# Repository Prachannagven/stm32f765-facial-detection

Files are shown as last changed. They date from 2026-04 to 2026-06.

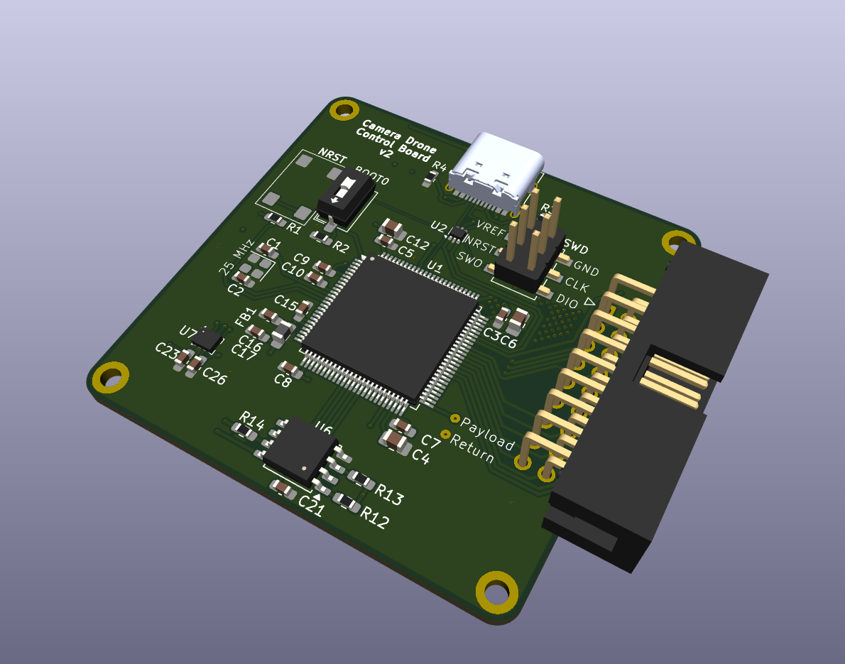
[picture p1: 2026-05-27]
pcb/kamikaze-drone/images/v2/3D_Angled.png

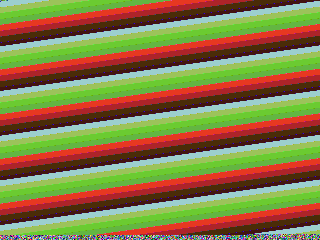
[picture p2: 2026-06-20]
firmware/ov7670_camera/Python/captures/20260612_212751.png

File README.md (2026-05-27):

# Introduction
The goal of this project is to build a 50x50mm drone, capable of autonomous flight, and recognizing humans. The final product should be able to fly towards the target.

For current protyping, I'm looking at using an OV7670 camera, which supplies up to a 320x260 frame, based on the qvga output. However, I can go as low as the qcif resolution (176x144), although I'm not sure recognition will work well on that.

# Links to Look at
[OV7670 Interfacing][https://www.youtube.com/watch?v=aanNau1RDTA]

# Hardware Design
I use an STM32F765VIT6 due to its on board DCMI block, as well as its ART accelerator to speed up computations. It pairs with a TOF sensor, a BMP280 barometer, IMU and magnetic field sensor for full attitude determination.

Four brushed DC motors are used for this system, allowing for lightweight control. The only limitation here is how heavy the entire system is going to be. It can carry approximately 100-200 grams, which is well within our weight budget.

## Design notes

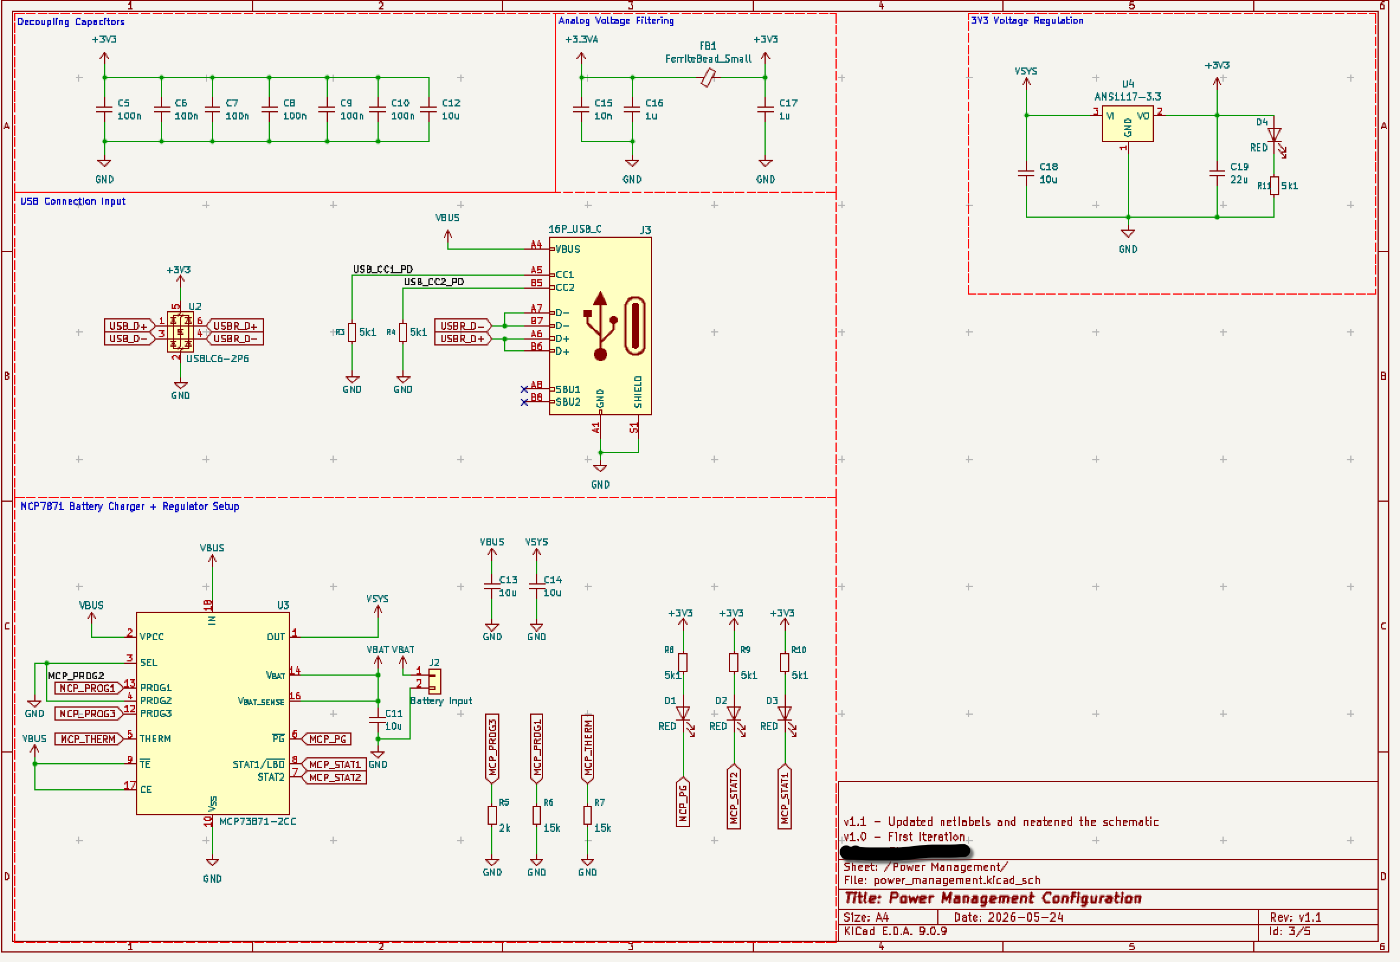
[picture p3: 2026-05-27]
pcb/kamikaze-drone/images/v2/Sch_PowerManagement.png

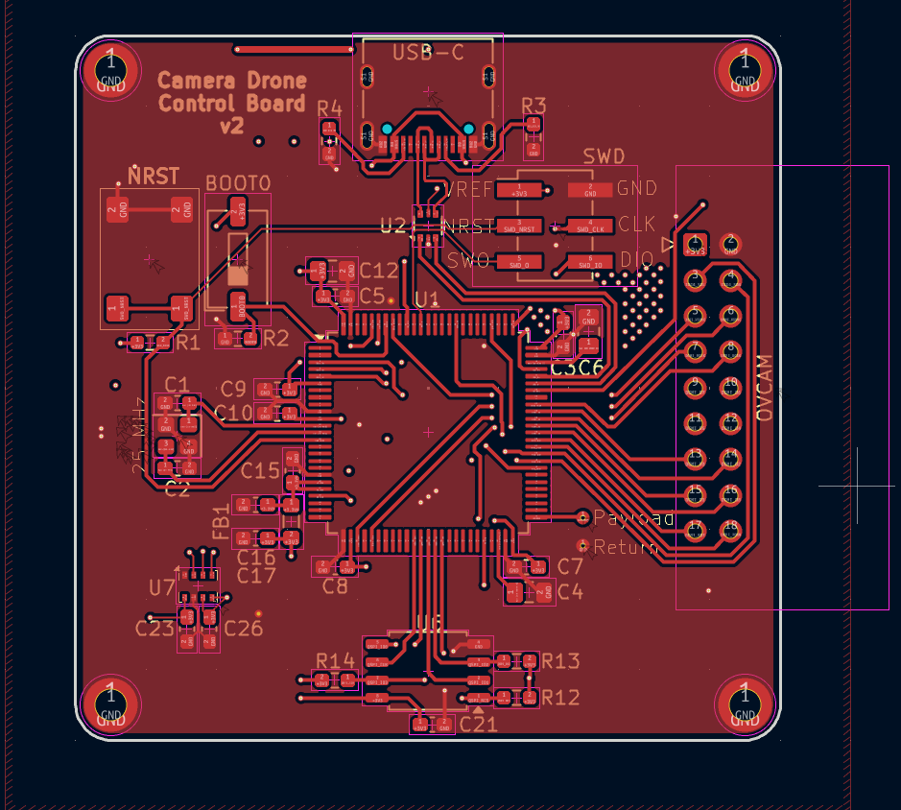
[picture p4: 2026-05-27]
pcb/kamikaze-drone/images/v2/PCB_FrontStandard.png

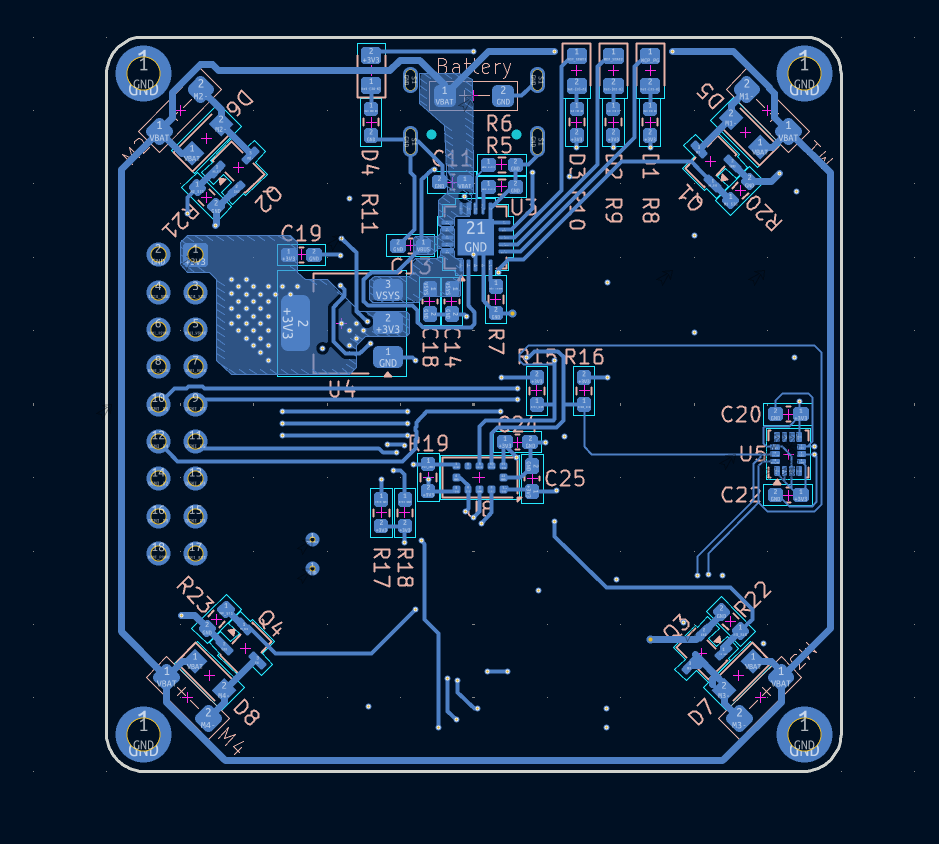
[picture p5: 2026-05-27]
pcb/kamikaze-drone/images/v2/PCB_BackStandard.png

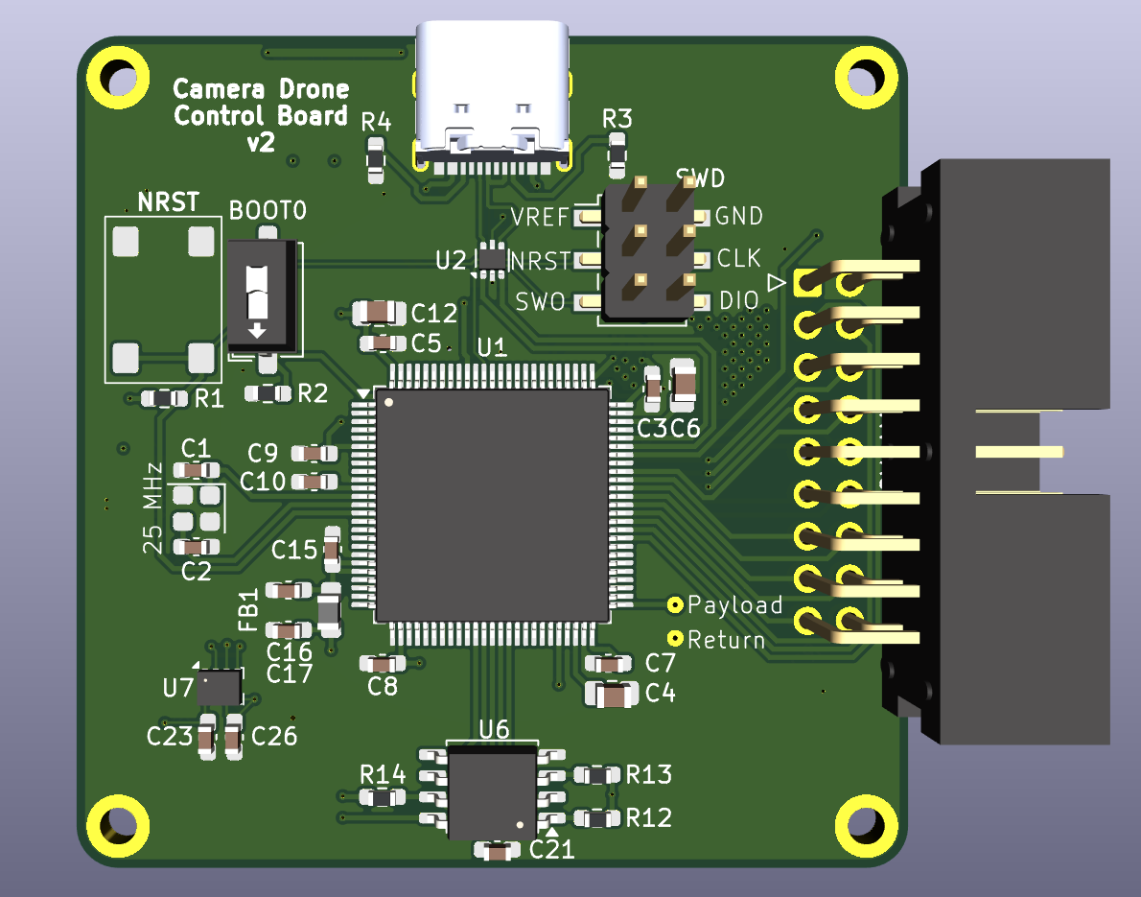
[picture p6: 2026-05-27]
pcb/kamikaze-drone/images/v2/3D_Front.png

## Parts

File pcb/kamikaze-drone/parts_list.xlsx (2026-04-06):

S. No. | Item | Spec | Cost | Communication Protocol | Link 1 | Vendor | Selected Comms
1 | Main MCU | STM32F765VIT6 | 794 | N/A | https://robu.in/product/stm32f765vit6-stmicroelectronics-arm-mcu-arm-cortex-m7-microcontrollers-arm-cortex-m7-32-bit-216-mhz-2-mb-100-pins/ | Robu | N/A
2 | IMU | LSM6DSLTR | 178 | SPI or I2C | https://robu.in/product/lsm6dsltr-stmicroelectronics-mems-module-inemo-lsm6d-series-imu-1-71-v-to-3-6-v-%c2%b1-16g-lga-14/ | Robu | I2C
3 | Barometer | BMP280 | 33 | I2C | https://robu.in/product/bmp280-barometric-pressure-and-altitude-sensor-i2c-spi-module/ | Robu | I2C
4 | EEPROM | M95512 | 62 | SPI | https://robu.in/product/m95512-rmn6p-eeprom-512-kbit-64k-x-8bit-serial-spi-16-mhz-soic-8-pins/ | Robu | SPI
5 | Magnetometer | QMC5883L | 317 | I2C | https://www.flyrobo.in/qmc5883l-qfn-16-three-axis-magnetic-sensor-chip?search=qmc5883l&description=true | FlyRobo | I2C
6 | GPS | Neo-6M | 272 | UART | https://robu.in/product/ublox-neo-6m-gps-module/ | Robu | UART
 | 16 Mhz Crystal | YSX321SL | 20 | N/A | https://robu.in/product/ysx321sl-16mhz-18pf-10ppm-4pins-smd-smt-metal-surface-quartz-crystal-pack-of-2/ | Robu | N/A
 | LDO | AMS1117-ADJ | 9 | N/A | https://robu.in/product/ams1117-adj-1a-sot-223-voltage-regulator-ic-pack-of-5-ics/
 |  |  | 1656

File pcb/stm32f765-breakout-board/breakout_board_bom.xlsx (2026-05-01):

Robu SKU | Reference | Qty | Value | Bought | Cost | Total
595331 | C1,C2 | 2 | 10p | 10 | 1.8 | 18 | 18
595344 | C3,C4,C5,C6,C7,C8,C13 | 9 | 100n | 50 | 0.7 | 35 | 53
1544904 | C9, C14, C15 | 1 | 10u | 10 | 13 | 130 | 183
595338 | C10 | 1 | 10n | 10 | 5 | 50 | 233
R139421 | C11,C12 | 2 | 1u | 20 | 1.34 | 26.8 | 259.8
R136885 | C16,C17 | 2 | 2.2u | 20 | 1.86 | 37.2 | 297
827887 | D1 | 1 | LED | 20 | 0.79 | 15.8 | 312.8
R112445 | FB1 | 1 | FerriteBead | 10 | 3 | 30 | 342.8
R243053 | J1 | 1 | 16P_USB_C | 10 | 29 | 290 | 632.8
1114172 | J3 | 1 | SWD | 5 | 5 | 25 | 657.8
1114172 | J4 | 1 | Conn_01x05 | 0 | 5 | 0 | 657.8
1114172 | J5 | 1 | Conn_01x04 | 0 | 5 | 0 | 657.8
1114172 | J6,J7 | 2 | Conn_01x12 | 0 | 5 | 0 | 657.8
1114172 | J8 | 1 | Conn_01x03 | 0 | 5 | 0 | 657.8
1114172 | J9 | 1 | Conn_I2C2 | 0 | 5 | 0 | 657.8
R242850 | R2 | 1 | 10k | 100 | 0.16 | 16 | 673.8
R143534 | R3,R6,R7 | 3 | 1k5 | 100 | 0.28 | 28 | 701.8
R218648 | R4,R5 | 2 | 5k1 | 50 | 0.68 | 34 | 735.8
1883759 | SW2 | 1 | SW_BOOT0 | 10 | 1.55 | 15.5 | 751.3
R151772 | U1 | 1 | STM32F765VIT6 | 2 | 794 | 1588 | 2339.3
R194437 | U2 | 1 | AMS1117-3.3 | 10 | 7 | 70 | 2409.3
R243041 | U3 | 1 | USBLC6-2SC6 | 10 | 6 | 60 | 2469.3
R233512 | Y1 | 1 | 16MHz | 10 | 10 | 100 | 2569.3
 |  |  |  |  | Parts Total | 2569.3
 |  |  |  |  | PCB Total | 981
 |  |  |  |  | Project Total | 3550.3

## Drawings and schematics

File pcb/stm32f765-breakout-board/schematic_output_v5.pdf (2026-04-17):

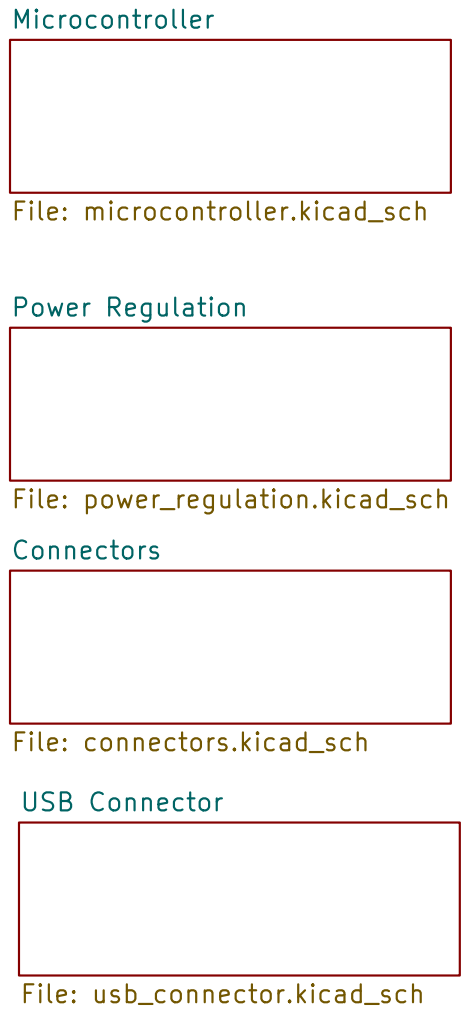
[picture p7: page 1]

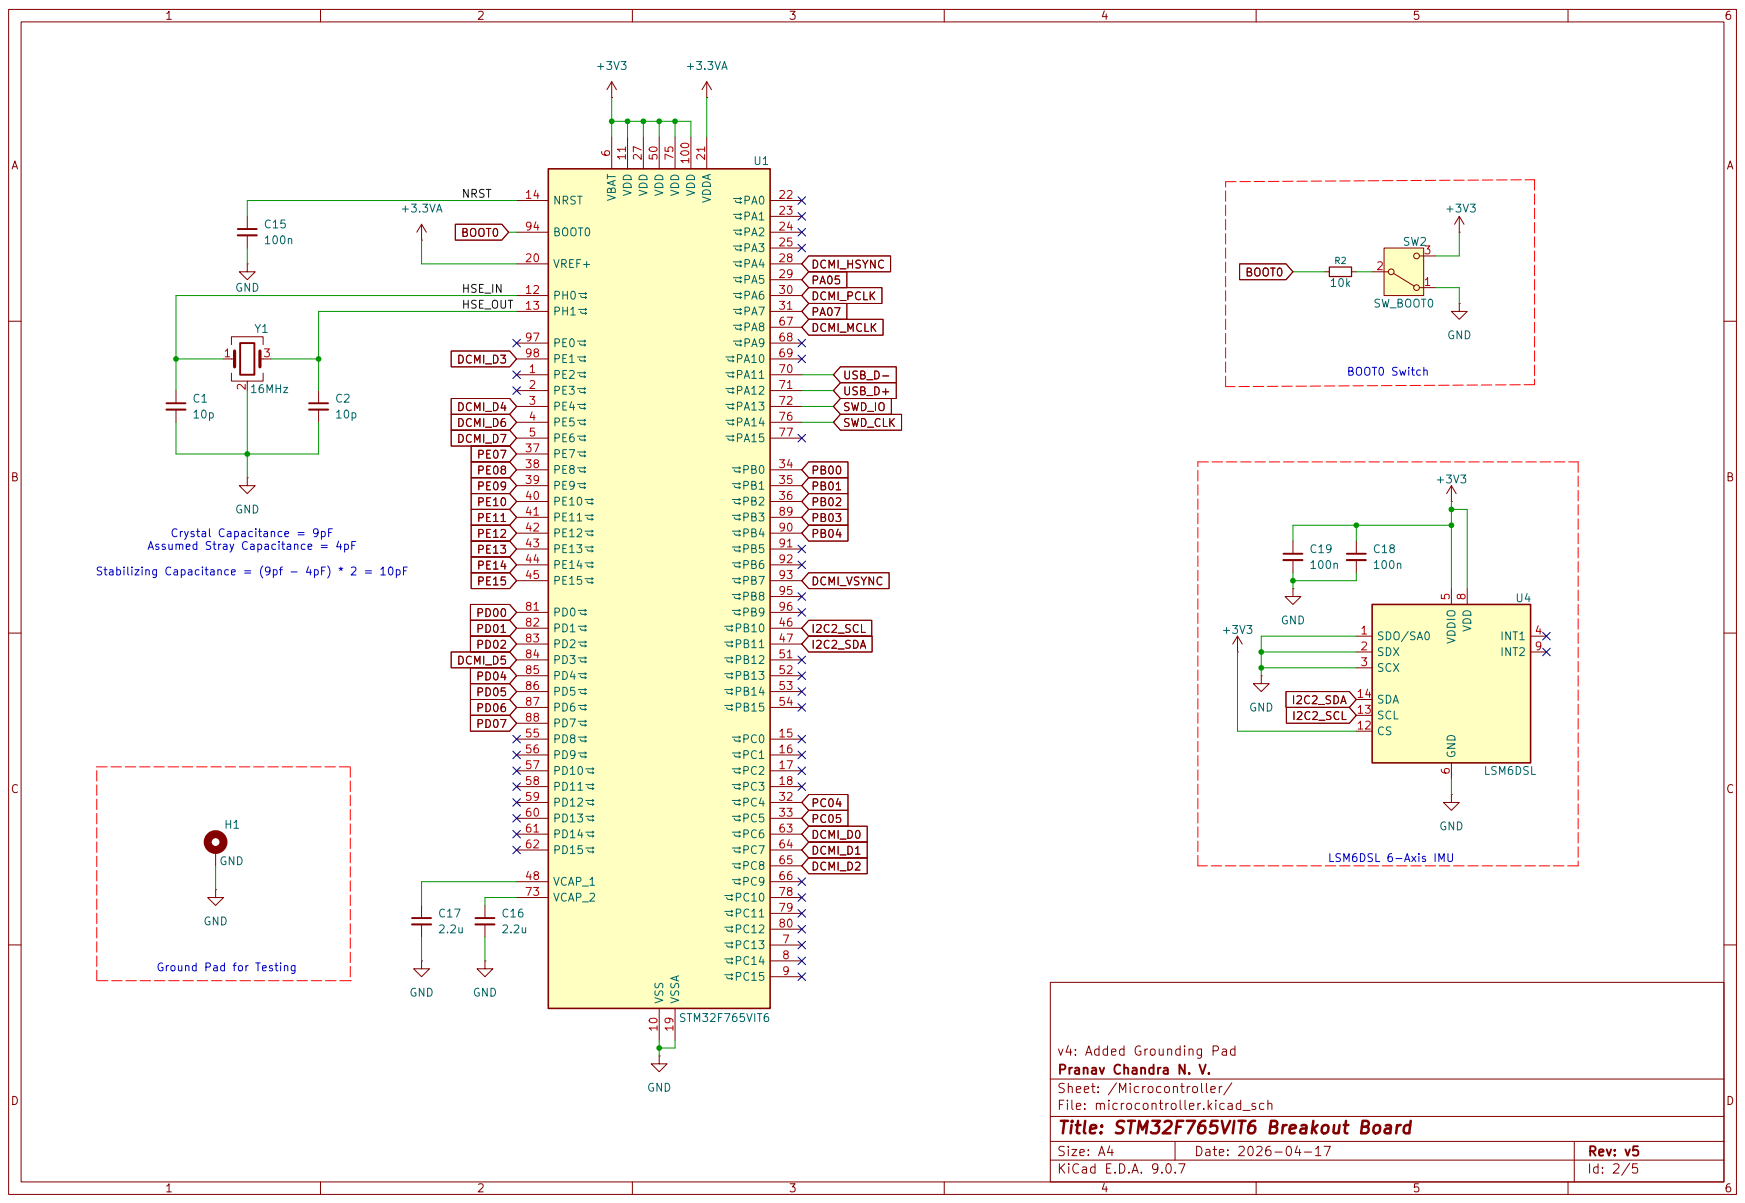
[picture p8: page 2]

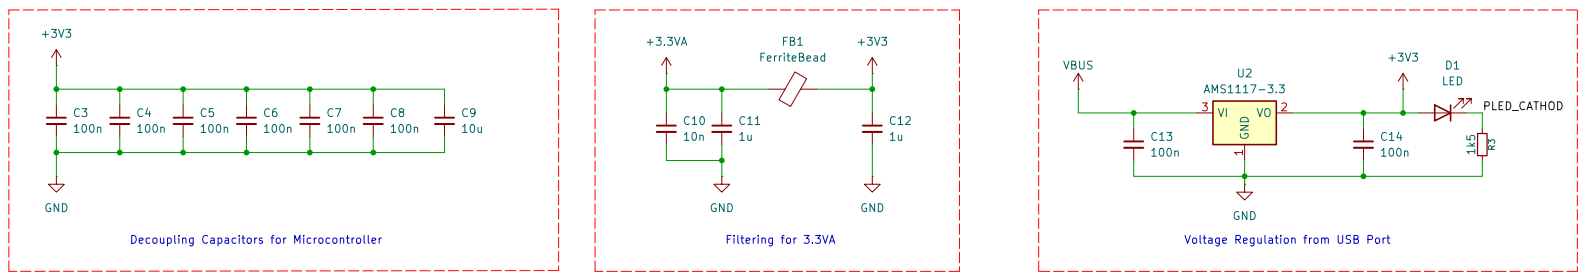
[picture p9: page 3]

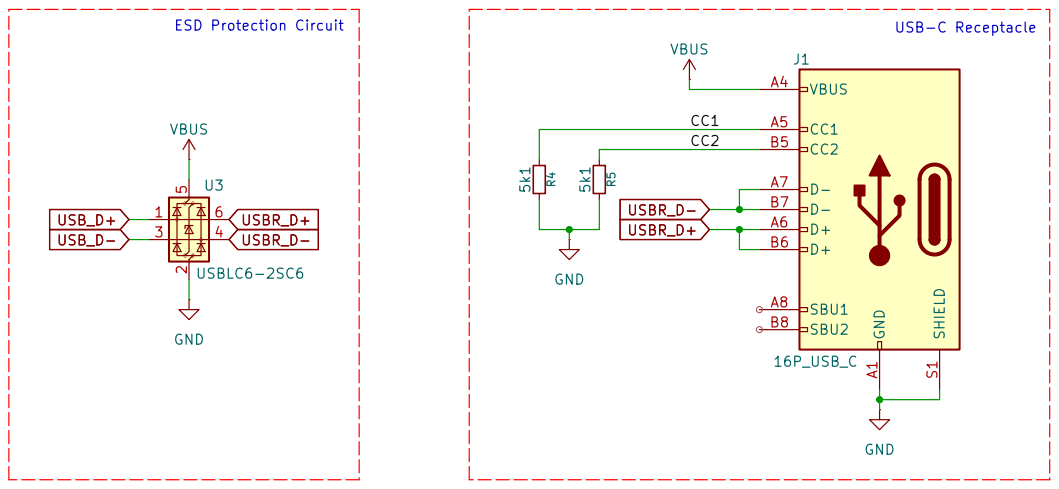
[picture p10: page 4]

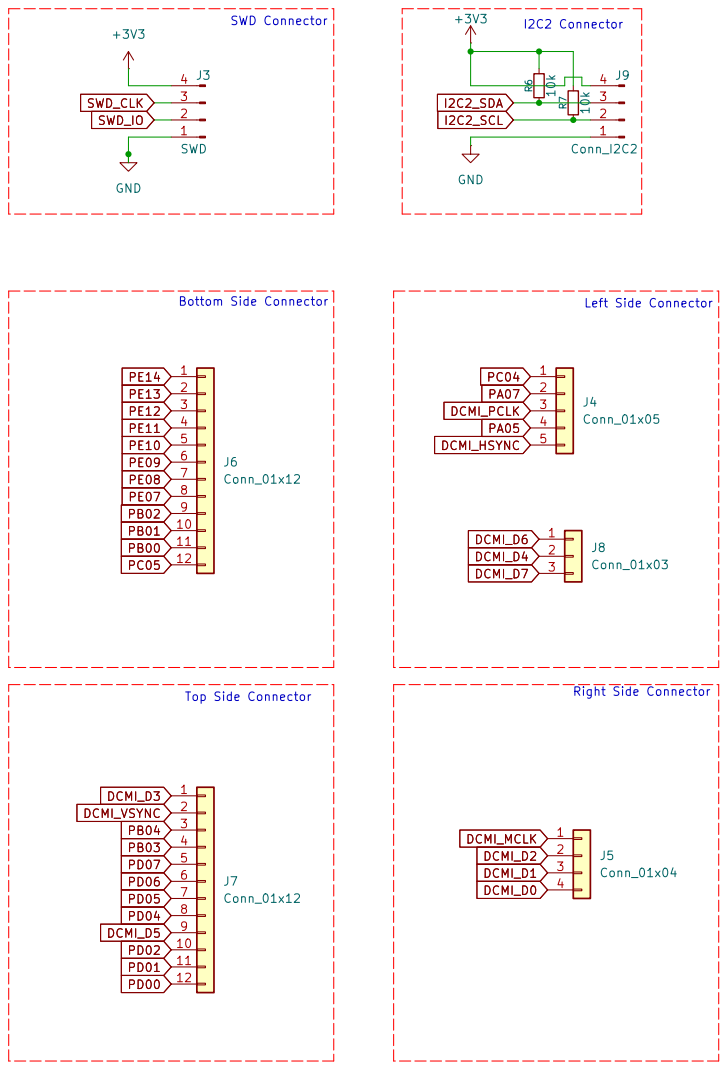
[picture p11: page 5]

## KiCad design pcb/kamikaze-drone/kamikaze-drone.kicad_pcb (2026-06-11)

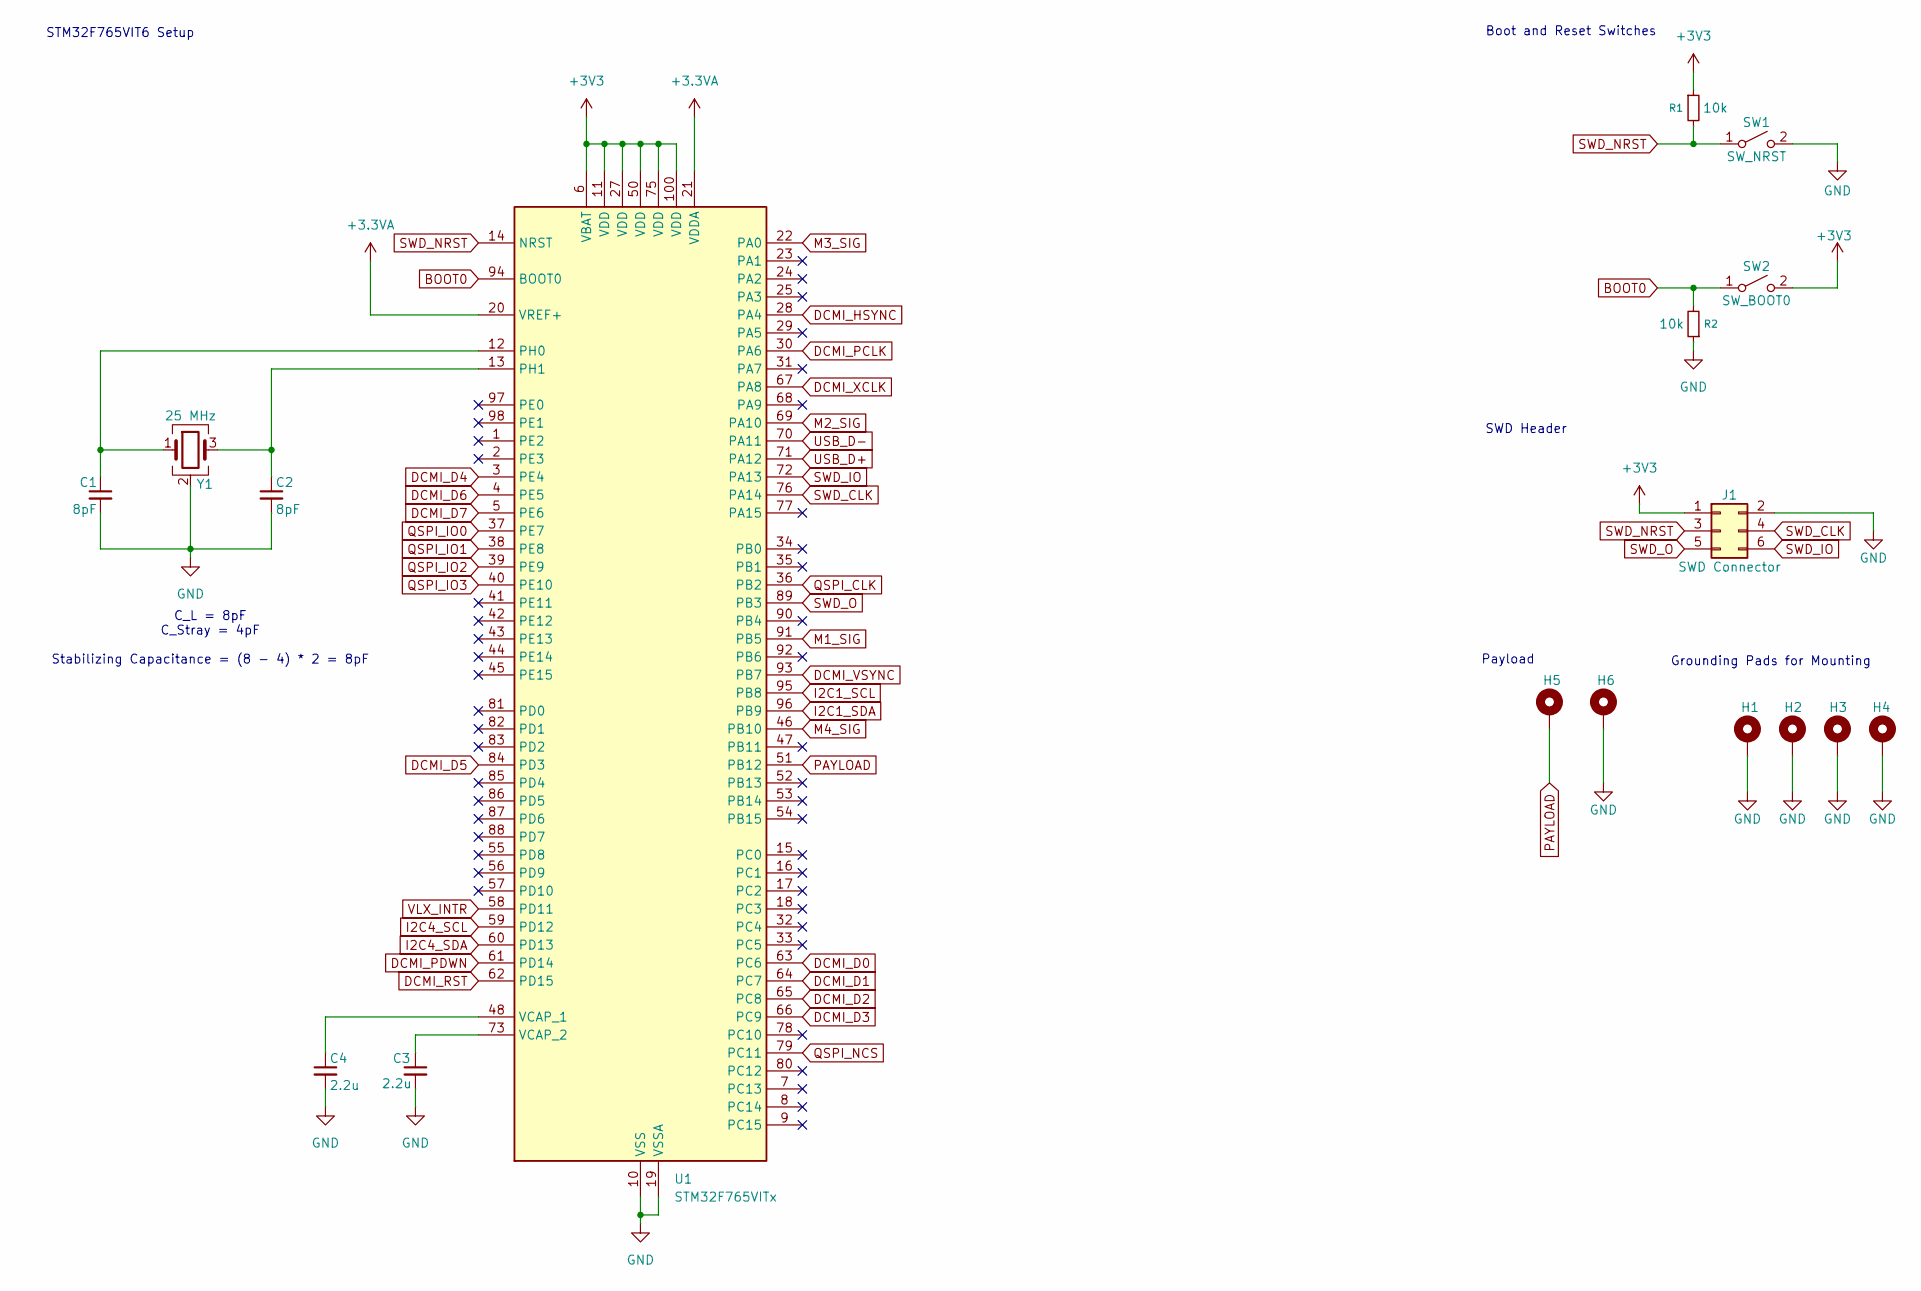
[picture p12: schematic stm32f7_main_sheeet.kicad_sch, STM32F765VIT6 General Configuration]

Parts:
C1, C2: 8pF; C_0603_1608Metric_Pad1.08x0.95mm_HandSolder
C3, C4: 2.2u; C_0805_2012Metric_Pad1.18x1.45mm_HandSolder
H1, H2, H3, H4: Gnd; MountingHole_2.2mm_M2_DIN965_Pad_TopBottom
H5, H6: Gnd; payload-pad
J1: SWD Connector; PinHeader_2x03_P2.54mm_Vertical_SMD
R1, R2: 10k; R_0603_1608Metric_Pad0.98x0.95mm_HandSolder
SW1: SW_NRST; button-footprint
SW2: SW_BOOT0; SW_DIP_SPSTx01_Slide_6.7x4.1mm_W6.73mm_P2.54mm_LowProfile_J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
U1: STM32F765VITx; LQFP-100_14x14mm_P0.5mm
Y1: 25 MHz; crysal-25MHz-2.55mm_x_2.05mm-2-4G

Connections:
+3.3VA: U1.20 (VREF+), U1.21 (VDDA); also elsewhere on the board
+3V3: J1.1, R1.1, SW2.2 (B), U1.6 (VBAT), U1.11 (VDD), U1.27 (VDD), U1.50 (VDD), U1.75 (VDD), U1.100 (VDD); also elsewhere on the board
BOOT0: R2.2, SW2.1 (A), U1.94 (BOOT0)
DCMI_D0: U1.63 (PC6); also elsewhere on the board
DCMI_D1: U1.64 (PC7); also elsewhere on the board
DCMI_D2: U1.65 (PC8); also elsewhere on the board
DCMI_D3: U1.66 (PC9); also elsewhere on the board
DCMI_D4: U1.3 (PE4); also elsewhere on the board
DCMI_D5: U1.84 (PD3); also elsewhere on the board
DCMI_D6: U1.4 (PE5); also elsewhere on the board
DCMI_D7: U1.5 (PE6); also elsewhere on the board
DCMI_HSYNC: U1.28 (PA4); also elsewhere on the board
DCMI_PCLK: U1.30 (PA6); also elsewhere on the board
DCMI_PDWN: U1.61 (PD14); also elsewhere on the board
DCMI_RST: U1.62 (PD15); also elsewhere on the board
DCMI_VSYNC: U1.93 (PB7); also elsewhere on the board
DCMI_XCLK: U1.67 (PA8); also elsewhere on the board
GND: C1.2, C2.2, C3.2, C4.2, H1.1, H2.1, H3.1, H4.1, H6.1, J1.2, R2.1, SW1.2 (B), U1.10 (VSS), U1.19 (VSSA), U1.26 (VSS), U1.49 (VSS), U1.74 (VSS), U1.99 (VSS), Y1.2 (G), Y1.4 (G); also elsewhere on the board
I2C1_SCL: U1.95 (PB8); also elsewhere on the board
I2C1_SDA: U1.96 (PB9); also elsewhere on the board
I2C4_SCL: U1.59 (PD12); also elsewhere on the board
I2C4_SDA: U1.60 (PD13); also elsewhere on the board
M1_SIG: U1.91 (PB5); also elsewhere on the board
M2_SIG: U1.69 (PA10); also elsewhere on the board
M3_SIG: U1.22 (PA0); also elsewhere on the board
M4_SIG: U1.46 (PB10); also elsewhere on the board
unnamed: C1.1, U1.12 (PH0), Y1.1
unnamed: C2.1, U1.13 (PH1), Y1.3
unnamed: C4.1, U1.48 (VCAP_1)
unnamed: C3.1, U1.73 (VCAP_2)
PAYLOAD: H5.1, U1.51 (PB12)
QSPI_CLK: U1.36 (PB2); also elsewhere on the board
QSPI_IO0: U1.37 (PE7); also elsewhere on the board
QSPI_IO1: U1.38 (PE8); also elsewhere on the board
QSPI_IO2: U1.39 (PE9); also elsewhere on the board
QSPI_IO3: U1.40 (PE10); also elsewhere on the board
QSPI_NCS: U1.79 (PC11); also elsewhere on the board
SWD_CLK: J1.4, U1.76 (PA14)
SWD_IO: J1.6, U1.72 (PA13)
SWD_NRST: J1.3, R1.2, SW1.1 (A), U1.14 (NRST)
SWD_O: J1.5, U1.89 (PB3)
USB_D+: U1.71 (PA12); also elsewhere on the board
USB_D-: U1.70 (PA11); also elsewhere on the board
VLX_INTR: U1.58 (PD11); also elsewhere on the board

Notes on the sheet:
Payload
Grounding Pads for Mounting
C_L = 8pF C_Stray = 4pF Stabilizing Capacitance = (8 - 4) * 2 = 8pF
Boot and Reset Switches
SWD Header
STM32F765VIT6 Setup

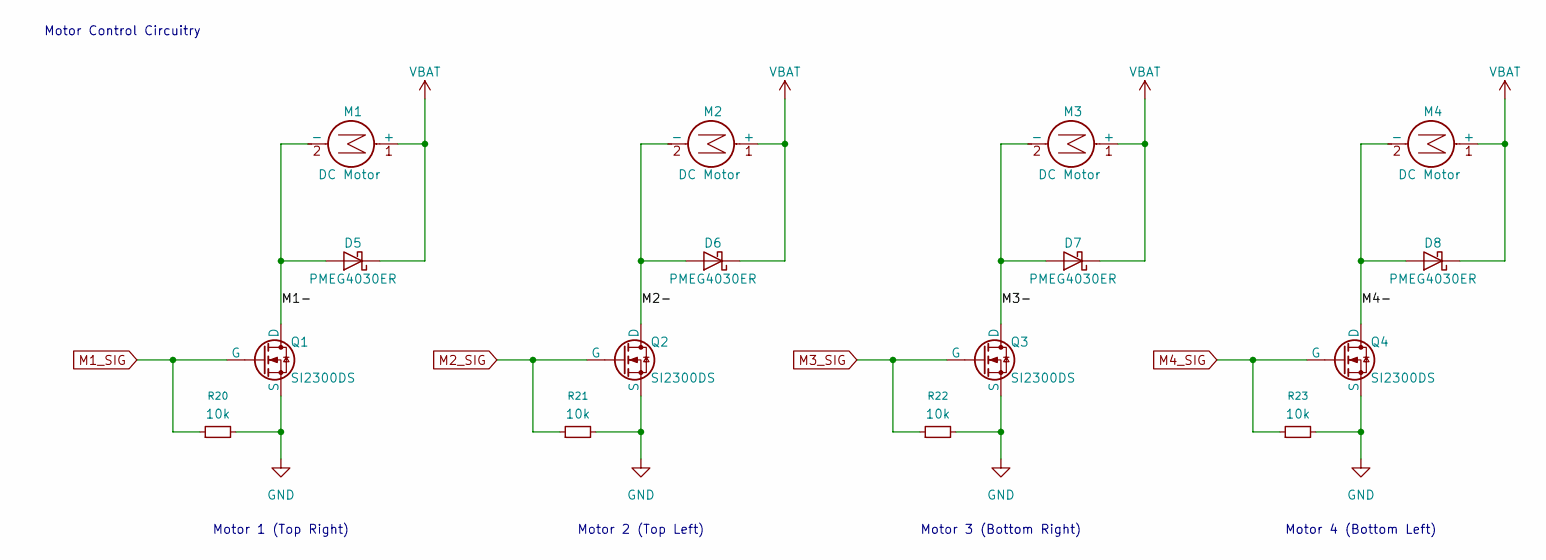
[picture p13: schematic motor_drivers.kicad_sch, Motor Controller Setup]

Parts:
D5, D6, D7, D8: PMEG4030ER; Nexperia_CFP3_SOD-123W
M1, M2, M3, M4: DC Motor; motor-attachment-pads
Q1, Q2, Q3, Q4: SI2300DS; SOT-23-3
R20, R21, R22, R23: 10k; R_0603_1608Metric_Pad0.98x0.95mm_HandSolder

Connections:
/Motors and Motor Drivers/M1-: D5.2 (A), M1.2 (-), Q1.3 (D)
/Motors and Motor Drivers/M2-: D6.2 (A), M2.2 (-), Q2.3 (D)
/Motors and Motor Drivers/M3-: D7.2 (A), M3.2 (-), Q3.3 (D)
/Motors and Motor Drivers/M4-: D8.2 (A), M4.2 (-), Q4.3 (D)
GND: Q1.2 (S), Q2.2 (S), Q3.2 (S), Q4.2 (S), R20.2, R21.2, R22.2, R23.2; also elsewhere on the board
M1_SIG: Q1.1 (G), R20.1; also elsewhere on the board
M2_SIG: Q2.1 (G), R21.1; also elsewhere on the board
M3_SIG: Q3.1 (G), R22.1; also elsewhere on the board
M4_SIG: Q4.1 (G), R23.1; also elsewhere on the board
VBAT: D5.1 (K), D6.1 (K), D7.1 (K), D8.1 (K), M1.1 (+), M2.1 (+), M3.1 (+), M4.1 (+); also elsewhere on the board

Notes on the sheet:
Motor 4 (Bottom Left)
Motor Control Circuitry
Motor 2 (Top Left)
Motor 1 (Top Right)
Motor 3 (Bottom Right)

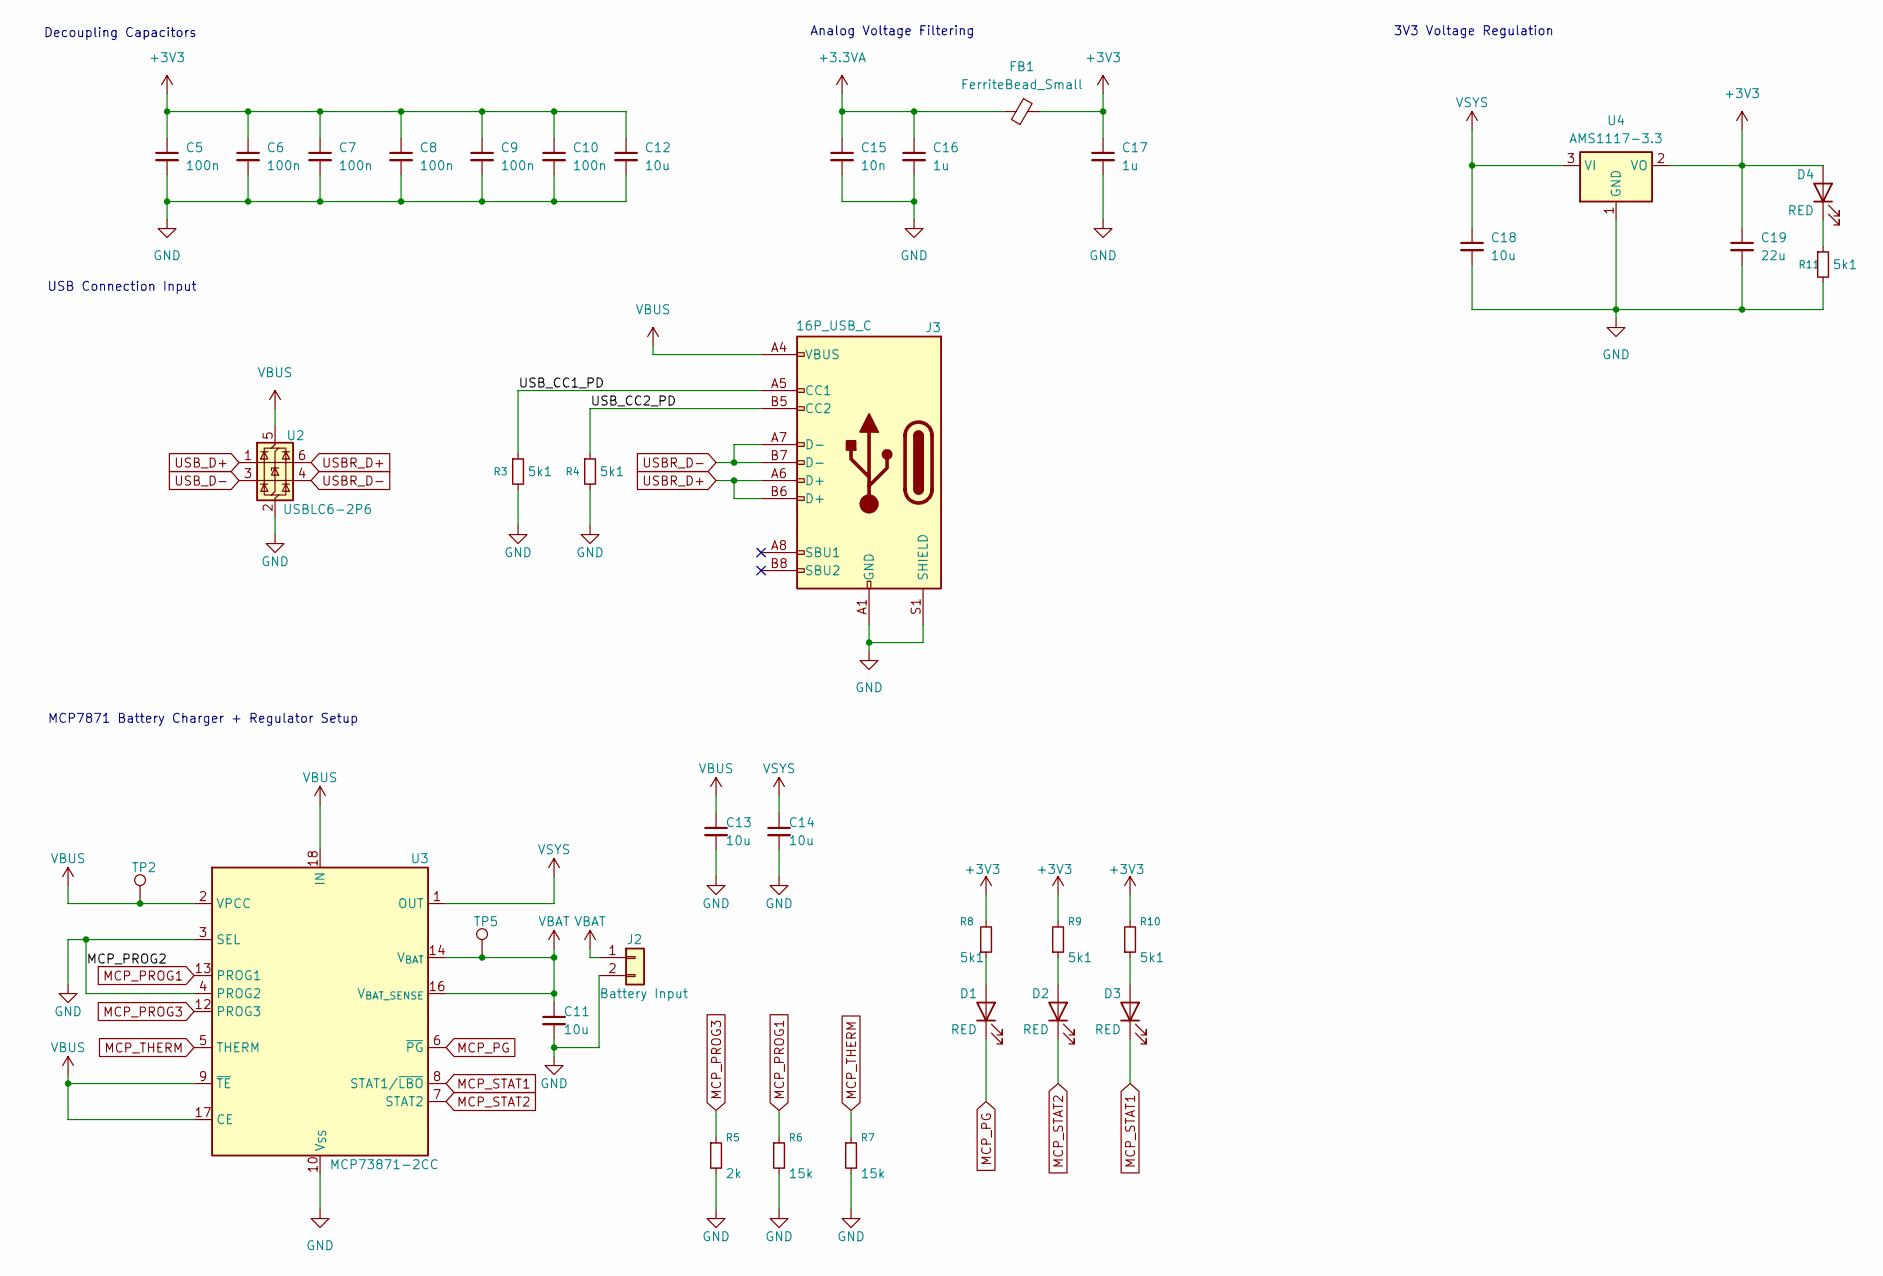
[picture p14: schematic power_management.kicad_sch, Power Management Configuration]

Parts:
C5, C6, C7, C8, C9, C10: 100n; C_0603_1608Metric_Pad1.08x0.95mm_HandSolder
C11, C13, C14, C18: 10u; C_0603_1608Metric_Pad1.08x0.95mm_HandSolder
C12: 10u; C_0805_2012Metric_Pad1.18x1.45mm_HandSolder
C15: 10n; C_0603_1608Metric_Pad1.08x0.95mm_HandSolder
C16, C17: 1u; C_0603_1608Metric_Pad1.08x0.95mm_HandSolder
C19: 22u; C_0603_1608Metric_Pad1.08x0.95mm_HandSolder
D1, D2, D3, D4: RED; LED_0805_2012Metric_Pad1.15x1.40mm_HandSolder
FB1: FerriteBead_Small; L_0805_2012Metric_Pad1.05x1.20mm_HandSolder
J2: Battery Input; motor-attachment-pads
J3: 16P_USB_C; USB_C_Receptacle_G-Switch_GT-USB-7010ASV
R3, R4, R8, R9, R10, R11: 5k1; R_0603_1608Metric_Pad0.98x0.95mm_HandSolder
R5: 2k; R_0603_1608Metric_Pad0.98x0.95mm_HandSolder
R6, R7: 15k; R_0603_1608Metric_Pad0.98x0.95mm_HandSolder
TP2, TP5: TestPoint; TestPoint_Pad_D1.0mm
U2: USBLC6-2P6; SOT-666
U3: MCP73871-2CC; QFN-20-1EP_4x4mm_P0.5mm_EP2.5x2.5mm
U4: AMS1117-3.3; SOT-223-3_TabPin2

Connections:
+3.3VA: C15.1, C16.1, FB1.1; also elsewhere on the board
+3V3: C5.1, C6.1, C7.1, C8.1, C9.1, C10.1, C12.1, C17.1, C19.1, D4.2 (A), FB1.2, R8.2, R9.2, R10.2, U4.2 (VO); also elsewhere on the board
/Power Management/USB_CC1_PD: J3.A5 (CC1), R3.1
/Power Management/USB_CC2_PD: J3.B5 (CC2), R4.1
GND: C5.2, C6.2, C7.2, C8.2, C9.2, C10.2, C11.2, C12.2, C13.2, C14.2, C15.2, C16.2, C17.2, C18.2, C19.2, J2.2, J3.A1 (GND), J3.A12 (GND), J3.B1 (GND), J3.B12 (GND), J3.S1 (SHIELD), R3.2, R4.2, R5.2, R6.2, R7.2, R11.2, U2.2 (GND), U3.3 (SEL), U3.4 (PROG2), U3.10 (V_{SS}), U3.11 (V_{SS}), U3.21 (V_{SS}), U4.1 (GND); also elsewhere on the board
MCP_PG: D1.1 (K), U3.6 (~PG)
MCP_PROG1: R6.1, U3.13 (PROG1)
MCP_PROG3: R5.1, U3.12 (PROG3)
MCP_STAT1: D3.1 (K), U3.8 (STAT1/~LBO)
MCP_STAT2: D2.1 (K), U3.7 (STAT2)
MCP_THERM: R7.1, U3.5 (THERM)
unnamed: D1.2 (A), R8.1
unnamed: D2.2 (A), R9.1
unnamed: D3.2 (A), R10.1
unnamed: D4.1 (K), R11.1
USBR_D+: J3.A6 (D+), J3.B6 (D+), U2.6 (I/O1)
USBR_D-: J3.A7 (D-), J3.B7 (D-), U2.4 (I/O2)
USB_D+: U2.1 (I/O1); also elsewhere on the board
USB_D-: U2.3 (I/O2); also elsewhere on the board
VBAT: C11.1, J2.1, TP5.1, U3.14 (V_{BAT}), U3.15 (V_{BAT}), U3.16 (V_{BAT_SENSE}); also elsewhere on the board
VBUS: C13.1, J3.A4 (VBUS), J3.A9 (VBUS), J3.B4 (VBUS), J3.B9 (VBUS), TP2.1, U2.5 (VBUS), U3.2 (VPCC), U3.9 (~TE), U3.17 (CE), U3.18 (IN), U3.19 (IN)
VSYS: C14.1, C18.1, U3.1 (OUT), U3.20 (OUT), U4.3 (VI)

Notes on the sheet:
MCP7871 Battery Charger + Regulator Setup
Analog Voltage Filtering
3V3 Voltage Regulation
USB Connection Input
Decoupling Capacitors

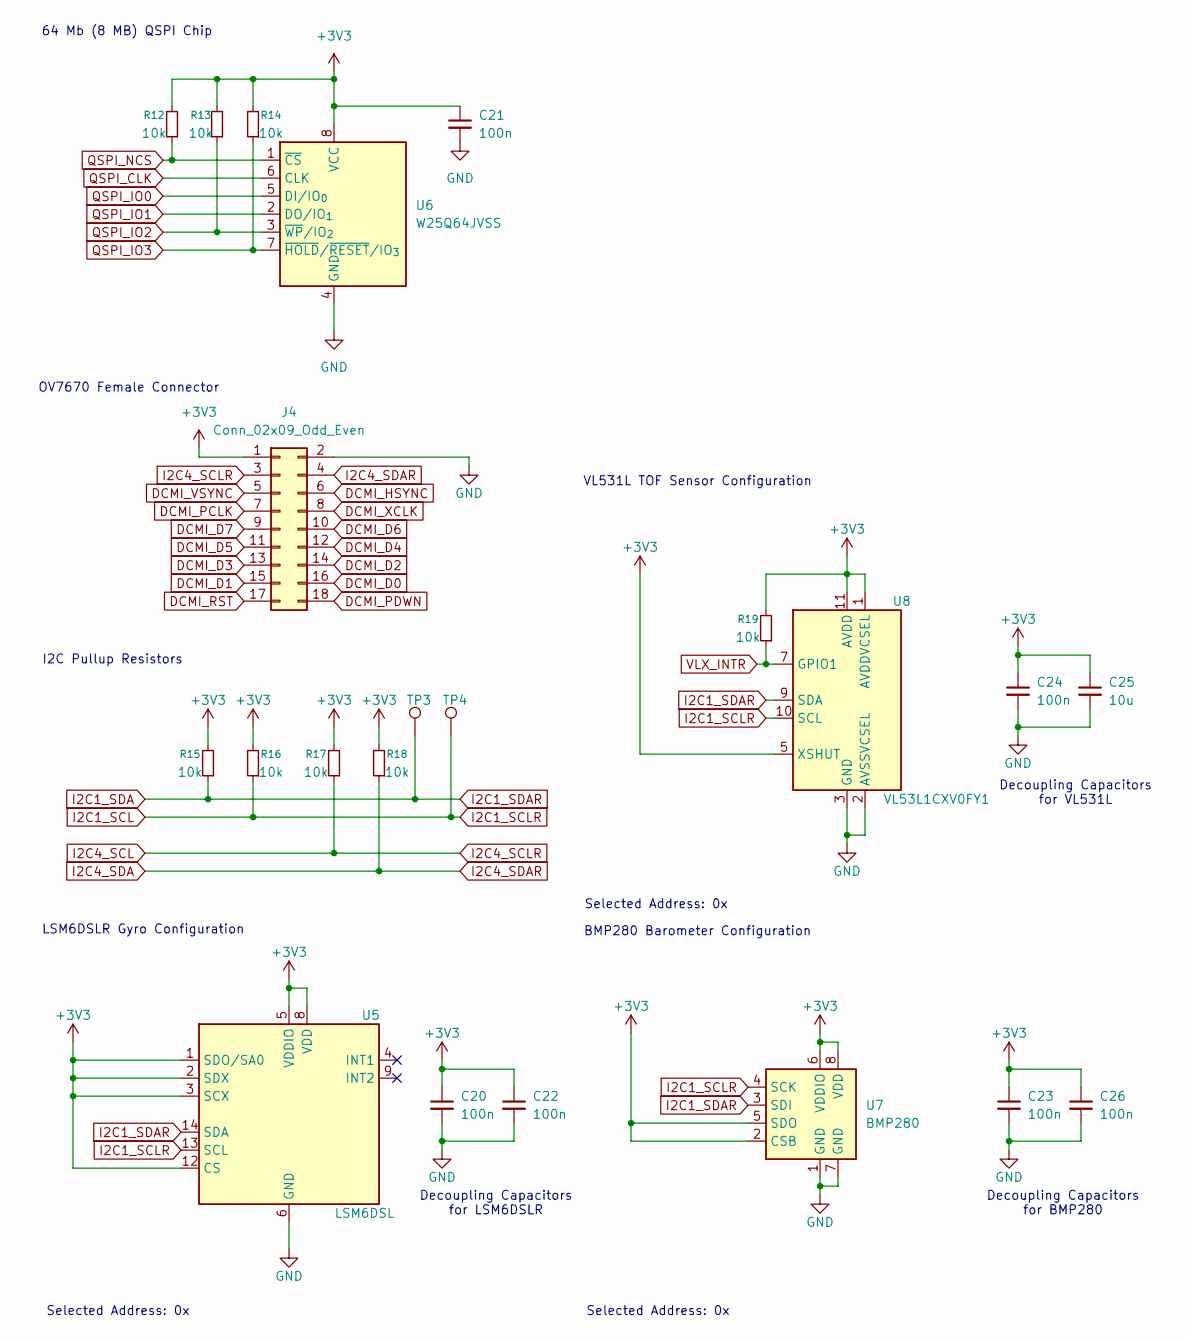
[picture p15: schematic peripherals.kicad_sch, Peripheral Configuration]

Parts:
C20, C21, C22, C23, C24, C26: 100n; C_0603_1608Metric_Pad1.08x0.95mm_HandSolder
C25: 10u; C_0603_1608Metric_Pad1.08x0.95mm_HandSolder
J4: Conn_02x09_Odd_Even; IDC-Header_2x09_P2.54mm_Horizontal
R12, R13, R14, R15, R16, R17, R18, R19: 10k; R_0603_1608Metric_Pad0.98x0.95mm_HandSolder
TP3, TP4: TestPoint; TestPoint_Pad_D1.0mm
U5: LSM6DSL; LGA-14_3x2.5mm_P0.5mm_LayoutBorder3x4y
U6: W25Q64JVSS; SOIC-8_5.3x5.3mm_P1.27mm
U7: BMP280; Bosch_LGA-8_2x2.5mm_P0.65mm_ClockwisePinNumbering
U8: VL53L1CXV0FY1; ST_VL53L1x

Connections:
+3V3: C20.1, C21.1, C22.1, C23.1, C24.1, C25.1, C26.1, J4.1, R12.2, R13.2, R14.2, R15.2, R16.2, R17.2, R18.2, R19.2, U5.1 (SDO/SA0), U5.2 (SDX), U5.3 (SCX), U5.5 (VDDIO), U5.8 (VDD), U5.12 (CS), U6.8 (VCC), U7.2 (CSB), U7.5 (SDO), U7.6 (VDDIO), U7.8 (VDD), U8.1 (AVDDVCSEL), U8.5 (XSHUT), U8.11 (AVDD); also elsewhere on the board
DCMI_D0: J4.16; also elsewhere on the board
DCMI_D1: J4.15; also elsewhere on the board
DCMI_D2: J4.14; also elsewhere on the board
DCMI_D3: J4.13; also elsewhere on the board
DCMI_D4: J4.12; also elsewhere on the board
DCMI_D5: J4.11; also elsewhere on the board
DCMI_D6: J4.10; also elsewhere on the board
DCMI_D7: J4.9; also elsewhere on the board
DCMI_HSYNC: J4.6; also elsewhere on the board
DCMI_PCLK: J4.7; also elsewhere on the board
DCMI_PDWN: J4.18; also elsewhere on the board
DCMI_RST: J4.17; also elsewhere on the board
DCMI_VSYNC: J4.5; also elsewhere on the board
DCMI_XCLK: J4.8; also elsewhere on the board
GND: C20.2, C21.2, C22.2, C23.2, C24.2, C25.2, C26.2, J4.2, U5.6 (GND), U5.7 (GND), U6.4 (GND), U7.1 (GND), U7.7 (GND), U8.2 (AVSSVCSEL), U8.3 (GND), U8.4 (GND), U8.6 (GND), U8.12 (GND); also elsewhere on the board
I2C1_SCL: R16.1, TP4.1, U5.13 (SCL), U7.4 (SCK), U8.10 (SCL); also elsewhere on the board
I2C1_SDA: R15.1, TP3.1, U5.14 (SDA), U7.3 (SDI), U8.9 (SDA); also elsewhere on the board
I2C4_SCL: J4.3, R17.1; also elsewhere on the board
I2C4_SDA: J4.4, R18.1; also elsewhere on the board
QSPI_CLK: U6.6 (CLK); also elsewhere on the board
QSPI_IO0: U6.5 (DI/IO_{0}); also elsewhere on the board
QSPI_IO1: U6.2 (DO/IO_{1}); also elsewhere on the board
QSPI_IO2: R13.1, U6.3 (~WP/IO_{2}); also elsewhere on the board
QSPI_IO3: R14.1, U6.7 (~HOLD/~RESET/IO_{3}); also elsewhere on the board
QSPI_NCS: R12.1, U6.1 (~CS); also elsewhere on the board
VLX_INTR: R19.1, U8.7 (GPIO1); also elsewhere on the board

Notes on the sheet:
I2C Pullup Resistors
Decoupling Capacitors for VL531L
64 Mb (8 MB) QSPI Chip
LSM6DSLR Gyro Configuration
Selected Address: 0x
Decoupling Capacitors for BMP280
VL531L TOF Sensor Configuration
Decoupling Capacitors for LSM6DSLR
BMP280 Barometer Configuration
OV7670 Female Connector

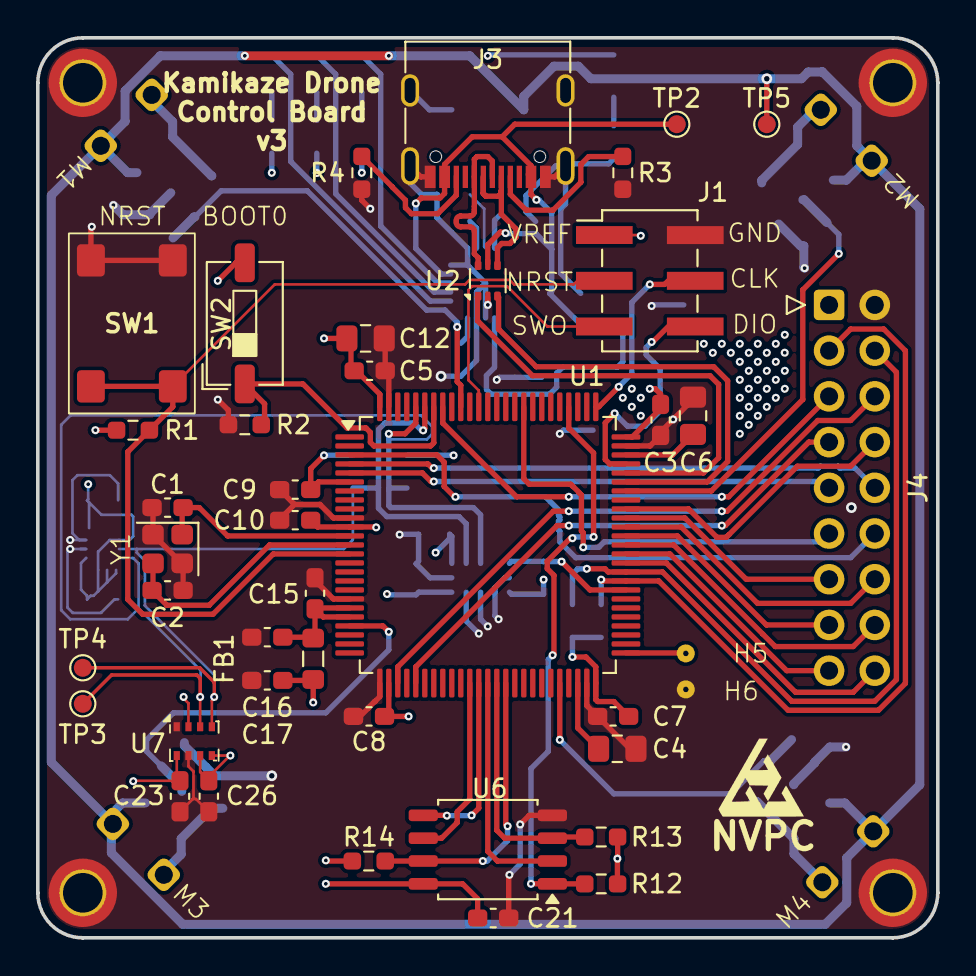
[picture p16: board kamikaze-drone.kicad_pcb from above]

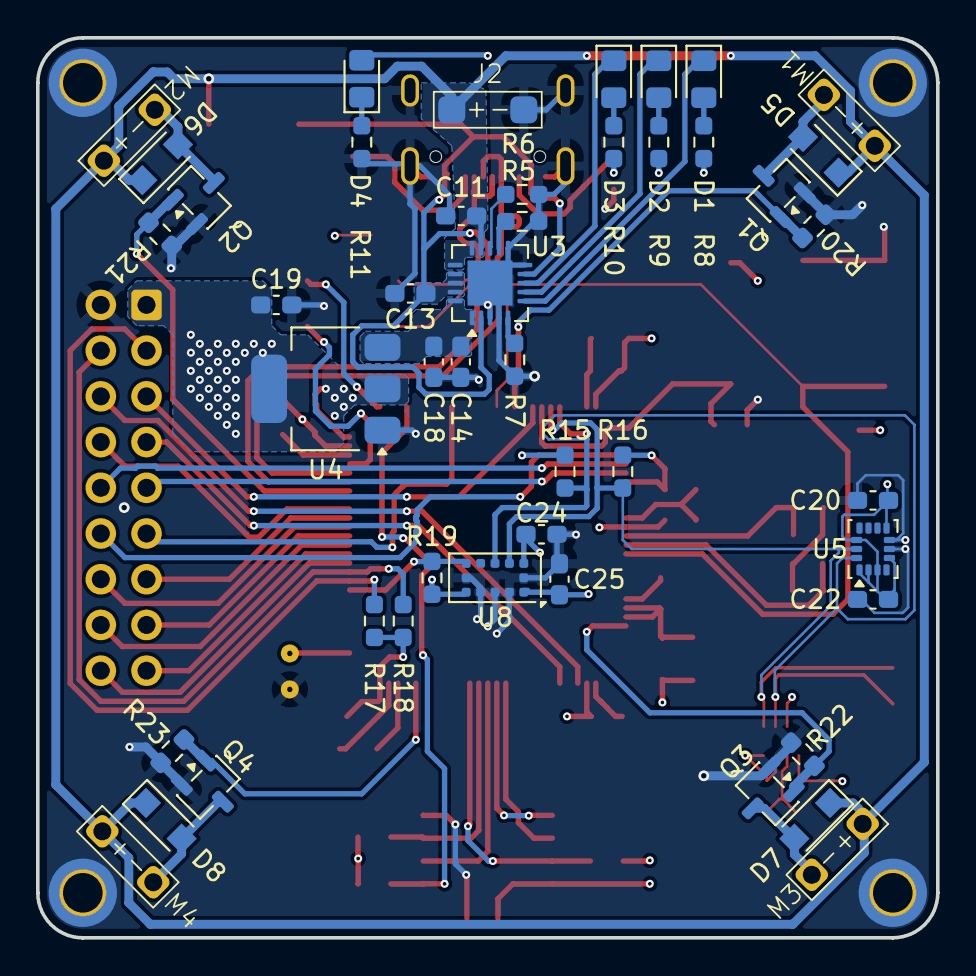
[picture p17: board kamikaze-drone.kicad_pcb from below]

Board: 4 copper layers, 50.0 x 50.0 mm, 92 parts (46 on the bottom side), 65 nets.

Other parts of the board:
NVPC: LOGO; logo

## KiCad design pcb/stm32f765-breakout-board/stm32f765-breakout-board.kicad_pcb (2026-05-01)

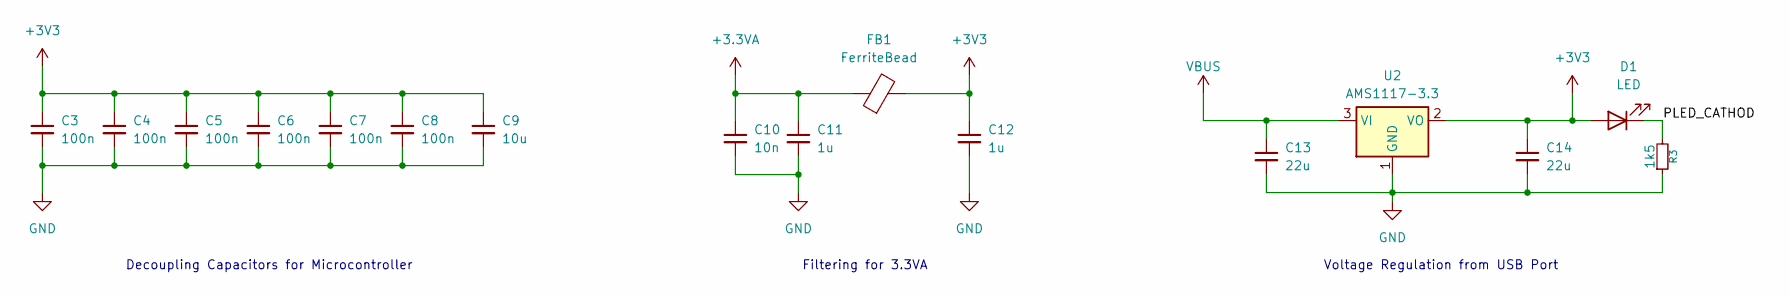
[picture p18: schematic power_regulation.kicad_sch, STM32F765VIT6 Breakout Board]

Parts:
C3, C4, C5, C6, C7, C8: 100n; C_0805_2012Metric_Pad1.18x1.45mm_HandSolder
C9: 10u; C_0805_2012Metric_Pad1.18x1.45mm_HandSolder
C10: 10n; C_0805_2012Metric_Pad1.18x1.45mm_HandSolder
C11, C12: 1u; C_0805_2012Metric_Pad1.18x1.45mm_HandSolder
C13, C14: 22u; C_0805_2012Metric_Pad1.18x1.45mm_HandSolder
D1: LED; LED_0805_2012Metric_Pad1.15x1.40mm_HandSolder
FB1: FerriteBead; L_0805_2012Metric_Pad1.05x1.20mm_HandSolder
R3: 1k5; R_0805_2012Metric_Pad1.20x1.40mm_HandSolder
U2: AMS1117-3.3; SOT-223-3_TabPin2

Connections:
+3.3VA: C10.1, C11.1, FB1.1; also elsewhere on the board
+3V3: C3.1, C4.1, C5.1, C6.1, C7.1, C8.1, C9.1, C12.1, C14.1, D1.2 (A), FB1.2, U2.2 (VO); also elsewhere on the board
/Power Regulation/PLED_CATHOD: D1.1 (K), R3.2
GND: C3.2, C4.2, C5.2, C6.2, C7.2, C8.2, C9.2, C10.2, C11.2, C12.2, C13.2, C14.2, R3.1, U2.1 (GND); also elsewhere on the board
VBUS: C13.1, U2.3 (VI); also elsewhere on the board

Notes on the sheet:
Filtering for 3.3VA
Voltage Regulation from USB Port
Decoupling Capacitors for Microcontroller

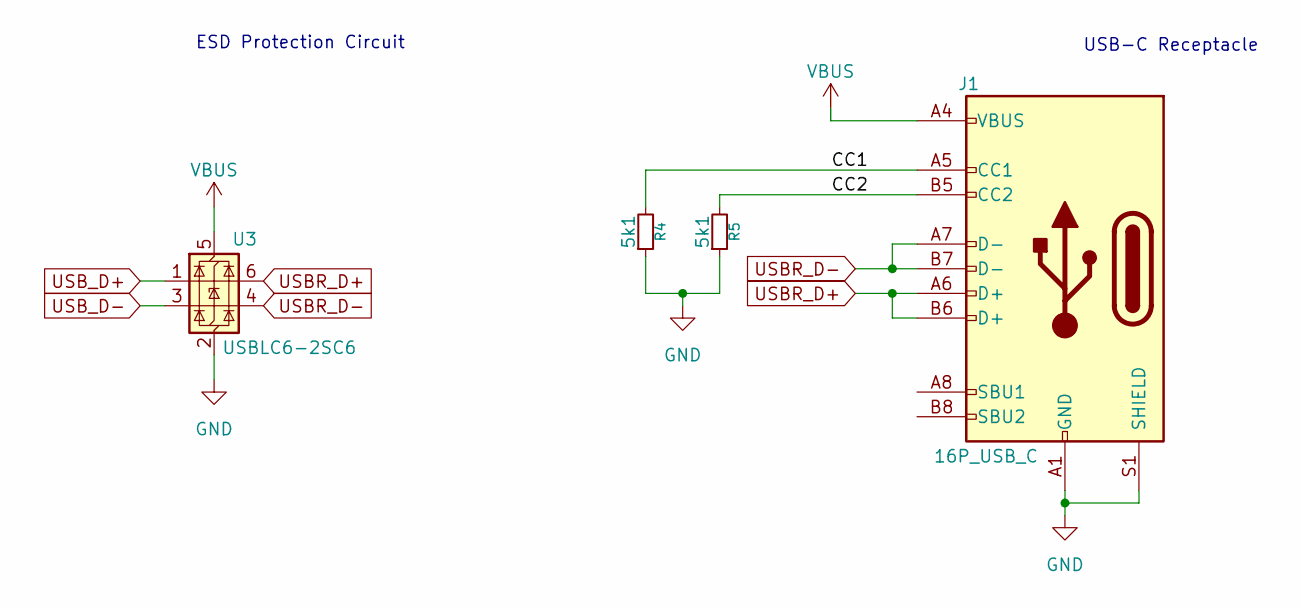
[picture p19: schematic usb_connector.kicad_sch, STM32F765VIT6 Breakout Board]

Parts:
J1: 16P_USB_C; USB_C_Receptacle_G-Switch_GT-USB-7010ASV
R4, R5: 5k1; R_0805_2012Metric_Pad1.20x1.40mm_HandSolder
U3: USBLC6-2SC6; SOT-23-6

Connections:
/USB Connector/CC1: J1.A5 (CC1), R4.2
/USB Connector/CC2: J1.B5 (CC2), R5.2
GND: J1.A1 (GND), J1.A12 (GND), J1.B1 (GND), J1.B12 (GND), J1.S1 (SHIELD), R4.1, R5.1, U3.2 (GND); also elsewhere on the board
USBR_D+: J1.A6 (D+), J1.B6 (D+), U3.6 (I/O1)
USBR_D-: J1.A7 (D-), J1.B7 (D-), U3.4 (I/O2)
USB_D+: U3.1 (I/O1); also elsewhere on the board
USB_D-: U3.3 (I/O2); also elsewhere on the board
VBUS: J1.A4 (VBUS), J1.A9 (VBUS), J1.B4 (VBUS), J1.B9 (VBUS), U3.5 (VBUS); also elsewhere on the board

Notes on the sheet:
USB-C Receptacle
ESD Protection Circuit

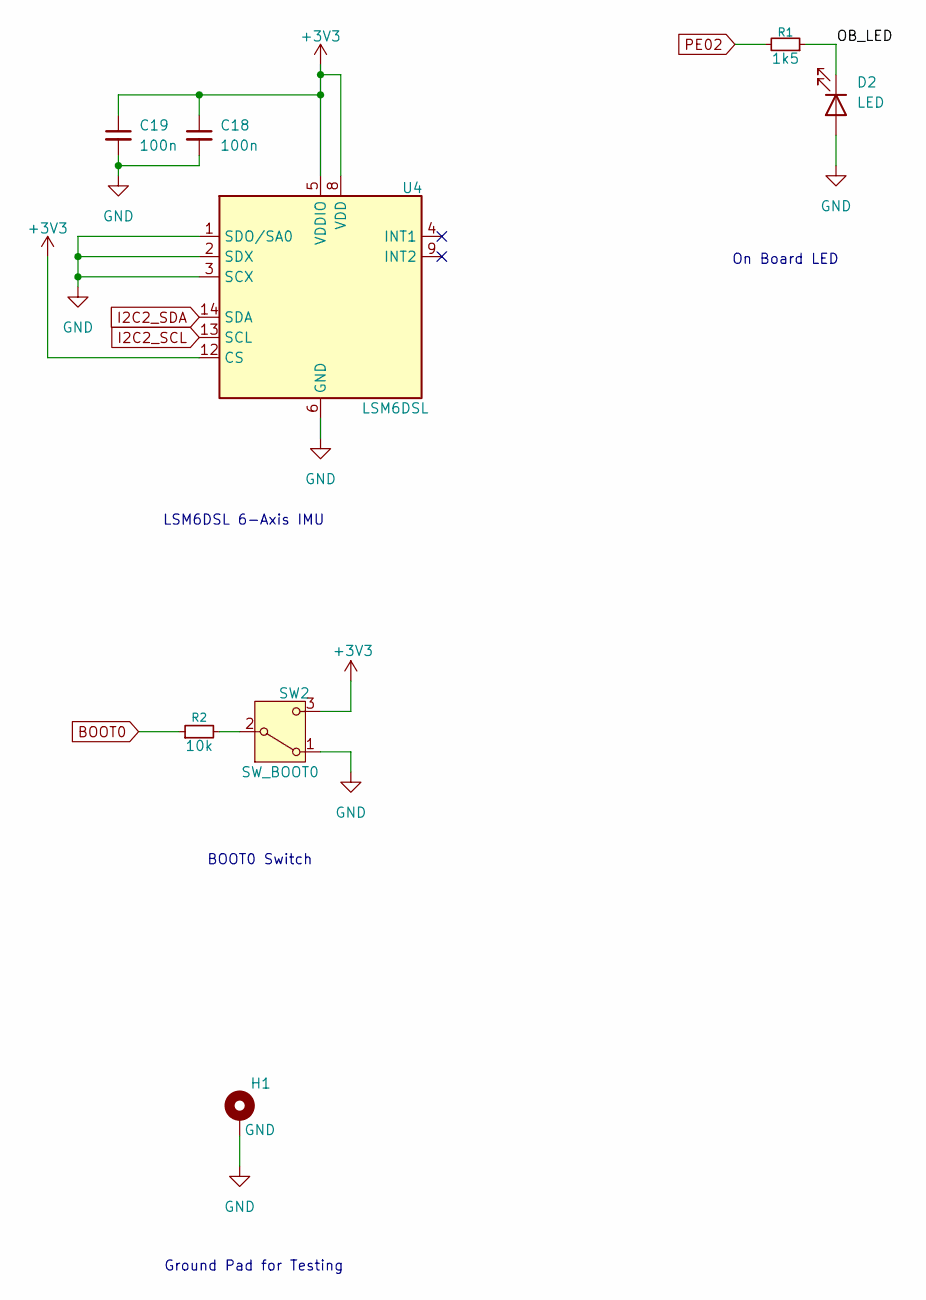
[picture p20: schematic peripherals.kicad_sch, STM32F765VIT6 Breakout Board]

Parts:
C18, C19: 100n; C_0805_2012Metric_Pad1.18x1.45mm_HandSolder
D2: LED; LED_0805_2012Metric_Pad1.15x1.40mm_HandSolder
H1: GND; MountingHole_2.2mm_M2_Pad
R1: 1k5; R_0805_2012Metric_Pad1.20x1.40mm_HandSolder
R2: 10k; R_0805_2012Metric_Pad1.20x1.40mm_HandSolder
SW2: SW_BOOT0; new_4.5x4.5_mm_tactile_button_1883759
U4: LSM6DSL; LGA-14_3x2.5mm_P0.5mm_LayoutBorder3x4y

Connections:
+3V3: C18.1, C19.1, SW2.3 (C), U4.5 (VDDIO), U4.8 (VDD), U4.12 (CS); also elsewhere on the board
/Peripherals/OB_LED: D2.1 (K), R1.1
BOOT0: R2.1; also elsewhere on the board
GND: C18.2, C19.2, D2.2 (A), H1.1, SW2.1 (A), U4.1 (SDO/SA0), U4.2 (SDX), U4.3 (SCX), U4.6 (GND), U4.7 (GND); also elsewhere on the board
I2C2_SCL: U4.13 (SCL); also elsewhere on the board
I2C2_SDA: U4.14 (SDA); also elsewhere on the board
unnamed: R2.2, SW2.2 (B)
PE02: R1.2; also elsewhere on the board

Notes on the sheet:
LSM6DSL 6-Axis IMU
Ground Pad for Testing
On Board LED
BOOT0 Switch

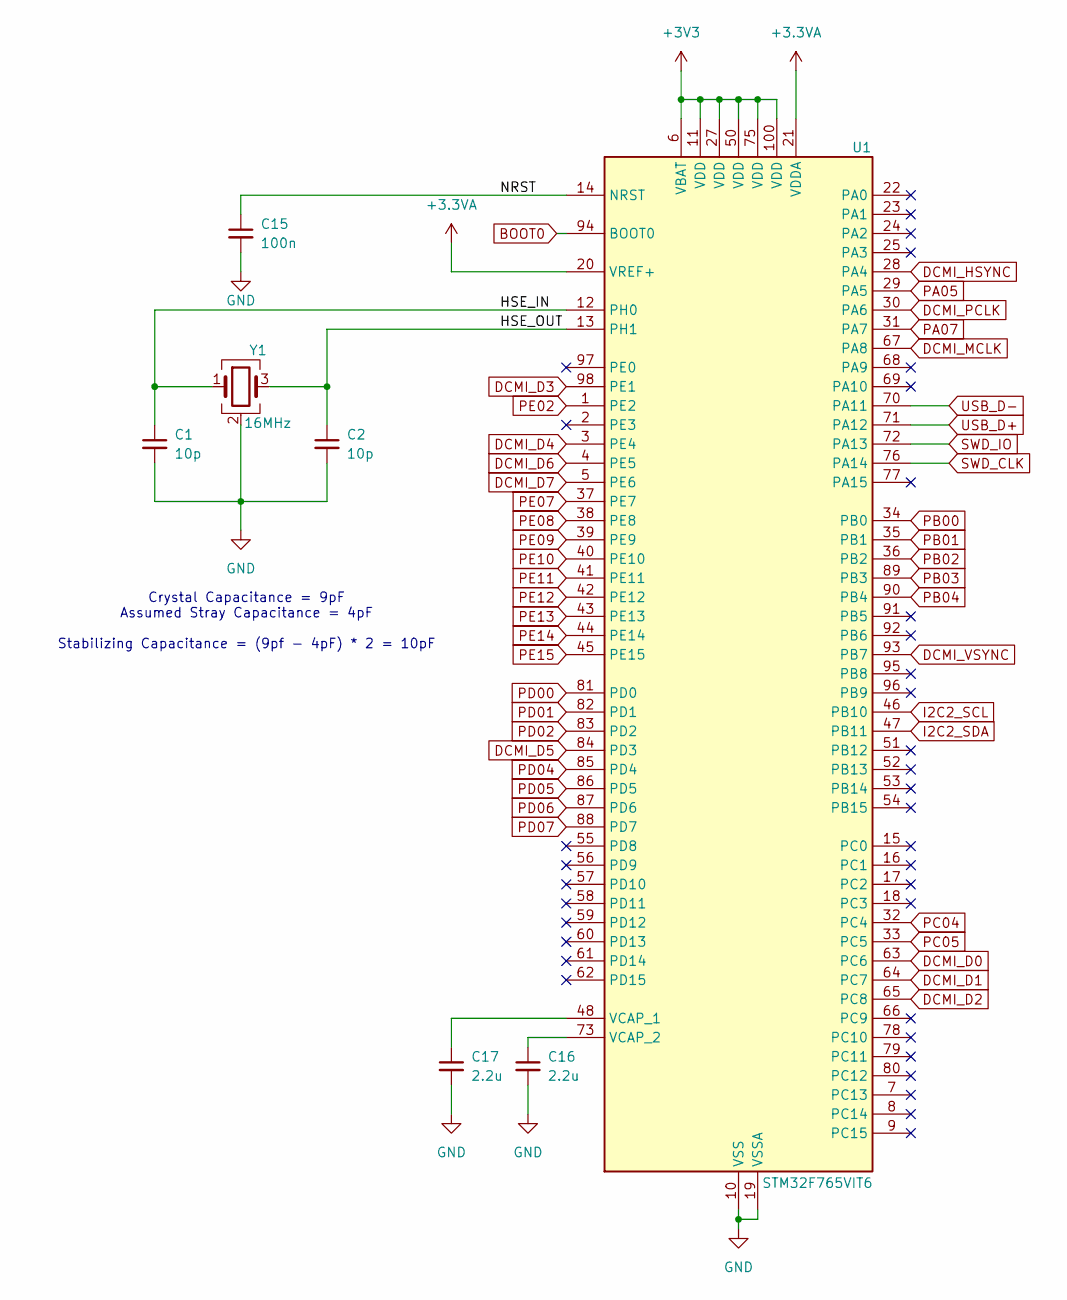
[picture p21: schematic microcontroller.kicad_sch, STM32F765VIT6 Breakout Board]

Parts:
C1, C2: 10p; C_0805_2012Metric_Pad1.18x1.45mm_HandSolder
C15: 100n; C_0805_2012Metric_Pad1.18x1.45mm_HandSolder
C16, C17: 2.2u; C_0805_2012Metric_Pad1.18x1.45mm_HandSolder
U1: STM32F765VIT6; LQFP-100_14x14mm_P0.5mm
Y1: 16MHz; Crystal_SMD_3225-4Pin_3.2x2.5mm_HandSoldering

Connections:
+3.3VA: U1.20 (VREF+), U1.21 (VDDA); also elsewhere on the board
+3V3: U1.6 (VBAT), U1.11 (VDD), U1.27 (VDD), U1.50 (VDD), U1.75 (VDD), U1.100 (VDD); also elsewhere on the board
/Microcontroller/HSE_IN: C1.1, U1.12 (PH0), Y1.1
/Microcontroller/HSE_OUT: C2.1, U1.13 (PH1), Y1.3
/Microcontroller/NRST: C15.1, U1.14 (NRST)
BOOT0: U1.94 (BOOT0); also elsewhere on the board
DCMI_D0: U1.63 (PC6); also elsewhere on the board
DCMI_D1: U1.64 (PC7); also elsewhere on the board
DCMI_D2: U1.65 (PC8); also elsewhere on the board
DCMI_D3: U1.98 (PE1); also elsewhere on the board
DCMI_D4: U1.3 (PE4); also elsewhere on the board
DCMI_D5: U1.84 (PD3); also elsewhere on the board
DCMI_D6: U1.4 (PE5); also elsewhere on the board
DCMI_D7: U1.5 (PE6); also elsewhere on the board
DCMI_HSYNC: U1.28 (PA4); also elsewhere on the board
DCMI_MCLK: U1.67 (PA8); also elsewhere on the board
DCMI_PCLK: U1.30 (PA6); also elsewhere on the board
DCMI_VSYNC: U1.93 (PB7); also elsewhere on the board
GND: C1.2, C2.2, C15.2, C16.2, C17.2, U1.10 (VSS), U1.19 (VSSA), U1.26 (VSS), U1.49 (VSS), U1.74 (VSS), U1.99 (VSS), Y1.2 (G), Y1.4 (G); also elsewhere on the board
I2C2_SCL: U1.46 (PB10); also elsewhere on the board
I2C2_SDA: U1.47 (PB11); also elsewhere on the board
unnamed: C17.1, U1.48 (VCAP_1)
unnamed: C16.1, U1.73 (VCAP_2)
PA05: U1.29 (PA5); also elsewhere on the board
PA07: U1.31 (PA7); also elsewhere on the board
PB00: U1.34 (PB0); also elsewhere on the board
PB01: U1.35 (PB1); also elsewhere on the board
PB02: U1.36 (PB2); also elsewhere on the board
PB03: U1.89 (PB3); also elsewhere on the board
PB04: U1.90 (PB4); also elsewhere on the board
PC04: U1.32 (PC4); also elsewhere on the board
PC05: U1.33 (PC5); also elsewhere on the board
PD00: U1.81 (PD0); also elsewhere on the board
PD01: U1.82 (PD1); also elsewhere on the board
PD02: U1.83 (PD2); also elsewhere on the board
PD04: U1.85 (PD4); also elsewhere on the board
PD05: U1.86 (PD5); also elsewhere on the board
PD06: U1.87 (PD6); also elsewhere on the board
PD07: U1.88 (PD7); also elsewhere on the board
PE02: U1.1 (PE2); also elsewhere on the board
PE07: U1.37 (PE7); also elsewhere on the board
PE08: U1.38 (PE8); also elsewhere on the board
PE09: U1.39 (PE9); also elsewhere on the board
PE10: U1.40 (PE10); also elsewhere on the board
PE11: U1.41 (PE11); also elsewhere on the board
PE12: U1.42 (PE12); also elsewhere on the board
PE13: U1.43 (PE13); also elsewhere on the board
PE14: U1.44 (PE14); also elsewhere on the board
PE15: U1.45 (PE15)
SWD_CLK: U1.76 (PA14); also elsewhere on the board
SWD_IO: U1.72 (PA13); also elsewhere on the board
USB_D+: U1.71 (PA12); also elsewhere on the board
USB_D-: U1.70 (PA11); also elsewhere on the board

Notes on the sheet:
Crystal Capacitance = 9pF Assumed Stray Capacitance = 4pF Stabilizing Capacitance = (9pf - 4pF) * 2 = 10pF

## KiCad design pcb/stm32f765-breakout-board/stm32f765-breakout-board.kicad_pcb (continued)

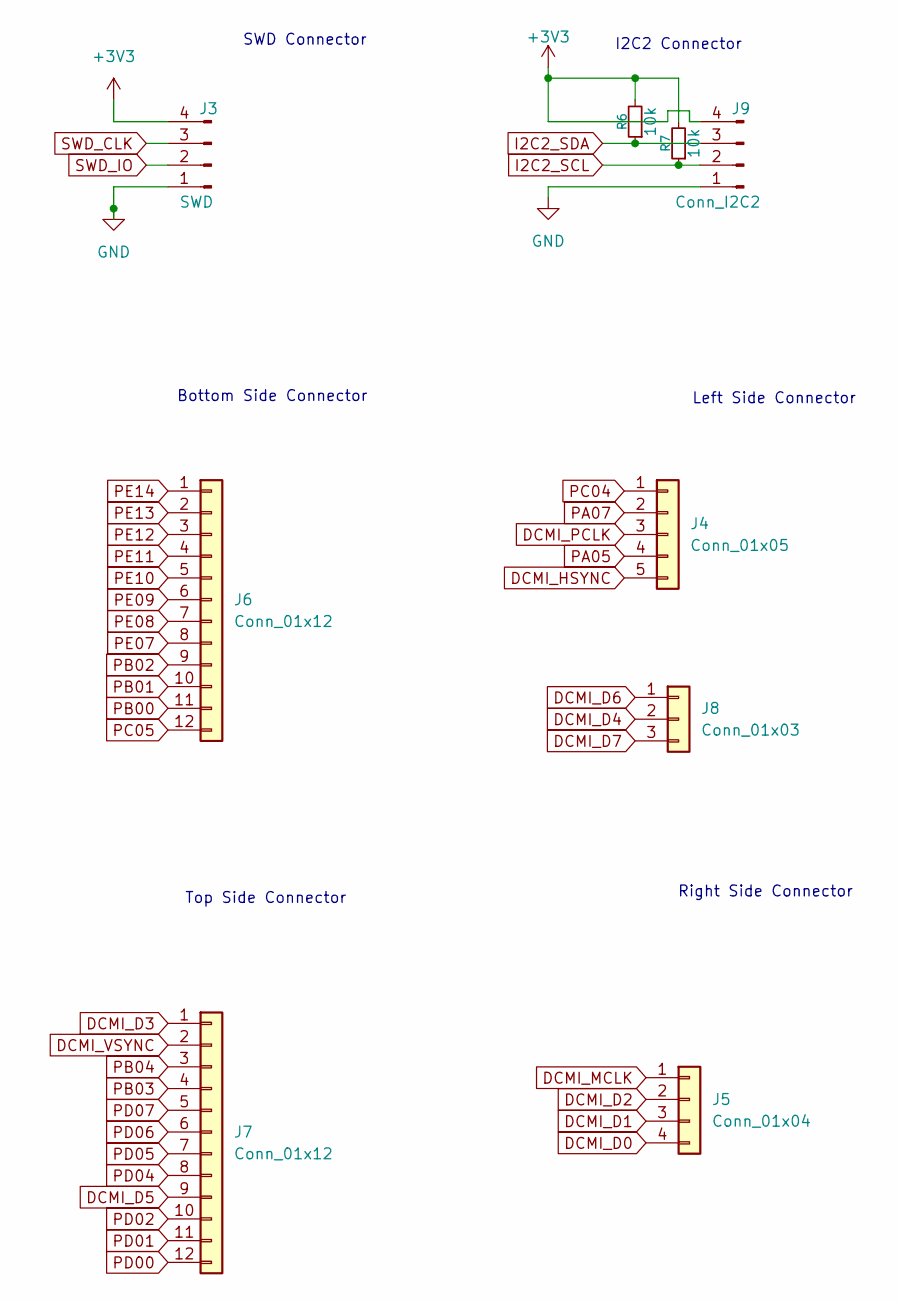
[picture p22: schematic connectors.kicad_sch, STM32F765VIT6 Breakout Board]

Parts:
J3: SWD; PinHeader_1x04_P2.54mm_Vertical
J4: Conn_01x05; PinHeader_1x05_P2.54mm_Vertical
J5: Conn_01x04; PinHeader_1x04_P2.54mm_Vertical
J6, J7: Conn_01x12; PinHeader_1x12_P2.54mm_Vertical
J8: Conn_01x03; PinHeader_1x03_P2.54mm_Vertical
J9: Conn_I2C2; PinHeader_1x04_P2.54mm_Vertical
R6, R7: 10k; R_0805_2012Metric_Pad1.20x1.40mm_HandSolder

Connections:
+3V3: J3.4, J9.4, R6.2, R7.2; also elsewhere on the board
DCMI_D0: J5.4; also elsewhere on the board
DCMI_D1: J5.3; also elsewhere on the board
DCMI_D2: J5.2; also elsewhere on the board
DCMI_D3: J7.1; also elsewhere on the board
DCMI_D4: J8.2; also elsewhere on the board
DCMI_D5: J7.9; also elsewhere on the board
DCMI_D6: J8.1; also elsewhere on the board
DCMI_D7: J8.3; also elsewhere on the board
DCMI_HSYNC: J4.5; also elsewhere on the board
DCMI_MCLK: J5.1; also elsewhere on the board
DCMI_PCLK: J4.3; also elsewhere on the board
DCMI_VSYNC: J7.2; also elsewhere on the board
GND: J3.1, J9.1; also elsewhere on the board
I2C2_SCL: J9.2, R7.1; also elsewhere on the board
I2C2_SDA: J9.3, R6.1; also elsewhere on the board
PA05: J4.4; also elsewhere on the board
PA07: J4.2; also elsewhere on the board
PB00: J6.11; also elsewhere on the board
PB01: J6.10; also elsewhere on the board
PB02: J6.9; also elsewhere on the board
PB03: J7.4; also elsewhere on the board
PB04: J7.3; also elsewhere on the board
PC04: J4.1; also elsewhere on the board
PC05: J6.12; also elsewhere on the board
PD00: J7.12; also elsewhere on the board
PD01: J7.11; also elsewhere on the board
PD02: J7.10; also elsewhere on the board
PD04: J7.8; also elsewhere on the board
PD05: J7.7; also elsewhere on the board
PD06: J7.6; also elsewhere on the board
PD07: J7.5; also elsewhere on the board
PE07: J6.8; also elsewhere on the board
PE08: J6.7; also elsewhere on the board
PE09: J6.6; also elsewhere on the board
PE10: J6.5; also elsewhere on the board
PE11: J6.4; also elsewhere on the board
PE12: J6.3; also elsewhere on the board
PE13: J6.2; also elsewhere on the board
PE14: J6.1; also elsewhere on the board
SWD_CLK: J3.3; also elsewhere on the board
SWD_IO: J3.2; also elsewhere on the board

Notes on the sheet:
I2C2 Connector
Top Side Connector
SWD Connector
Bottom Side Connector
Left Side Connector
Right Side Connector

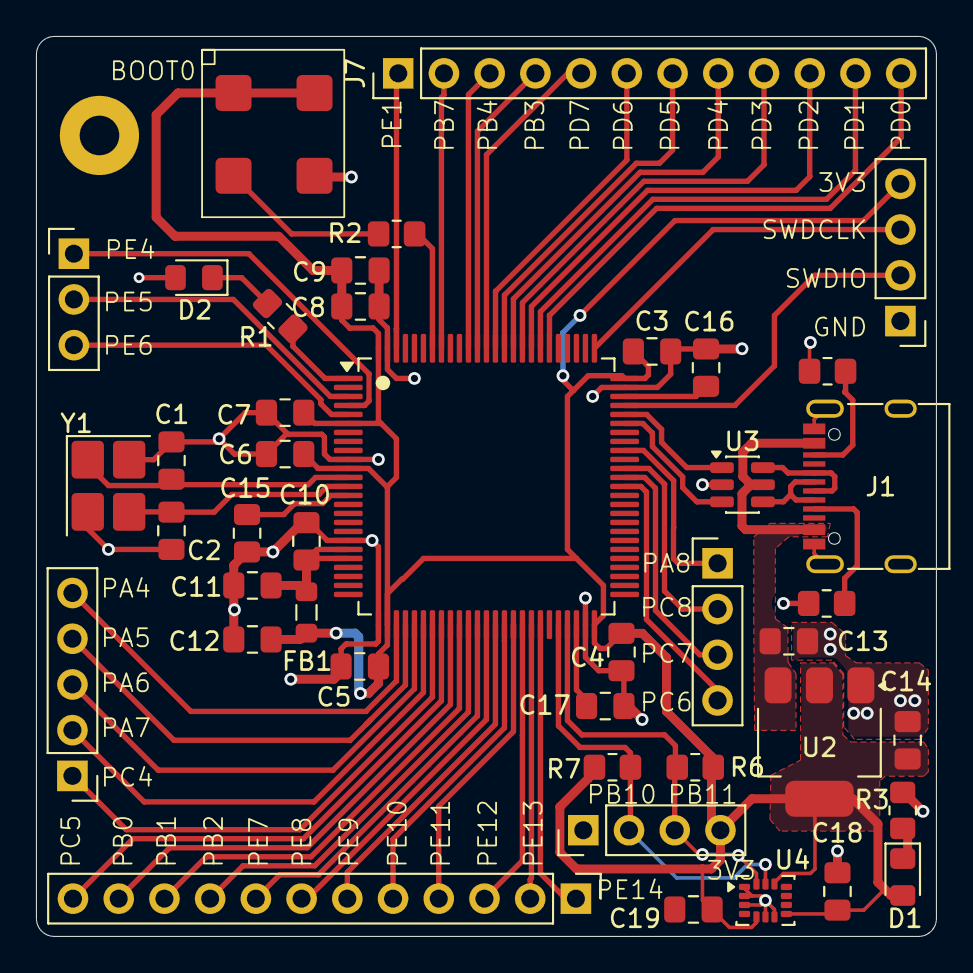
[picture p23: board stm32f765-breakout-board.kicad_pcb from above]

Board: 2 copper layers, 50.0 x 50.0 mm, 44 parts (0 on the bottom side), 60 nets.

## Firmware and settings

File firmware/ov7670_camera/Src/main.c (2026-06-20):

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
/* Includes ------------------------------------------------------------------*/
#include "main.h"
#include "usb_device.h"

/* USER CODE BEGIN Includes */
#include "my_usb.h"
#include "usbd_cdc_if.h"
#include <stdint.h>
/* USER CODE END Includes */

/* USER CODE BEGIN PD */
#define CHUNK_SIZE 512
#define OV7670_ADDR (0x21 << 1)
#ifndef MIN
#define MIN(a, b) ((a) < (b) ? (a) : (b))
#endif
/* USER CODE END PD */


DCMI_HandleTypeDef hdcmi;
DMA_HandleTypeDef hdma_dcmi;

I2C_HandleTypeDef hi2c2;

/* USER CODE BEGIN PV */
volatile uint8_t frame_ready = 0;
uint8_t frame_buffer[320 * 240 * 2] __attribute__((section(".sram")));

/* USER CODE END PV */

void SystemClock_Config(void);
static void MPU_Config(void);
static void MX_GPIO_Init(void);
static void MX_DMA_Init(void);
static void MX_DCMI_Init(void);
static void MX_I2C2_Init(void);
/* USER CODE BEGIN PFP */
void HAL_DCMI_FrameEventCallback(DCMI_HandleTypeDef* hdcmi);
void capture_and_send(void);
void OV7670_HardwareReset(void);
uint8_t OV7670_ReadReg(uint8_t reg);
void OV7670_WriteReg(uint8_t reg, uint8_t value);
void send_frame_usb(void);
static void OV7670_Init_QVGA_RGB565(void);
static void OV7670_BarsTest(void);
/* USER CODE END PFP */

/**
 * @brief  The application entry point.
 * @retval int
 */
int main(void) {

    /* MPU Configuration--------------------------------------------------------*/
    MPU_Config();

    /* MCU Configuration--------------------------------------------------------*/

    /* Reset of all peripherals, Initializes the Flash interface and the Systick. */
    HAL_Init();

    /* Configure the system clock */
    SystemClock_Config();

    /* Initialize all configured peripherals */
    MX_GPIO_Init();
    MX_DMA_Init();
    MX_DCMI_Init();
    MX_I2C2_Init();
    MX_USB_DEVICE_Init();
    /* USER CODE BEGIN 2 */
    HAL_Delay(3000);

    USB_Print("Resetting OV7670 Camera\r\n");
    OV7670_HardwareReset();
    USB_Print("Validating PID and Version of OV7670 Camera\r\n");
    uint8_t pid = OV7670_ReadReg(0x0A);
    uint8_t ver = OV7670_ReadReg(0x0B);
    USB_Print("PID: %02X VER: %02X\r\n", pid, ver);

    if (pid == 0x76) {
        USB_Print("OV7670 detected\r\n");

        OV7670_Init_QVGA_RGB565();

        USB_Print("OV7670 configured\r\n");
    } else {
        USB_Print("Camera not detected\r\n");
        exit(-1);
    }

    USB_Print("COM7  = %02X\r\n", OV7670_ReadReg(0x12));
    USB_Print("CLKRC = %02X\r\n", OV7670_ReadReg(0x11));
    USB_Print("COM15 = %02X\r\n", OV7670_ReadReg(0x40));
    USB_Print("RGB444= %02X\r\n", OV7670_ReadReg(0x8C));

    USB_Print("Beginning Capture and Transmit Sequence with OV7670\r\n");
    OV7670_Init_QVGA_RGB565();
    USB_Print("Performing Bar Test");
    OV7670_BarsTest();
    /* USER CODE END 2 */

    /* Infinite loop */
    /* USER CODE BEGIN WHILE */
    while (1) {
        USB_Print("Sending Frame!!!!!!");
        capture_and_send();
        send_frame_usb();
        USB_Print("Frame sent\r\n");
        HAL_Delay(1000);
        /* USER CODE END WHILE */

        /* USER CODE BEGIN 3 */
    }
    /* USER CODE END 3 */
}

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
/* USER CODE BEGIN 4 */
void HAL_DCMI_FrameEventCallback(DCMI_HandleTypeDef* hdcmi) {
    // USB_Print("Frame callback\r\n");
    frame_ready = 1;
}

void capture_and_send(void) {
    frame_ready = 0;

    // Start single-frame capture via DMA
    if (HAL_DCMI_Start_DMA(&hdcmi, DCMI_MODE_SNAPSHOT, (uint32_t)frame_buffer,
                           (320 * 240 * 2) / 4) != HAL_OK) {
        USB_Print("DCMI DMA start failed\r\n");
        return;
    }
    // Wait for frame
    uint32_t start = HAL_GetTick();

    while (!frame_ready) {
        if (HAL_GetTick() - start > 3000) {
            USB_Print("Frame timeout\r\n");
            HAL_DCMI_Stop(&hdcmi);
            return;
        }
    }
    SCB_InvalidateDCache_by_Addr((uint32_t*)frame_buffer, sizeof(frame_buffer));
}

void send_frame_usb(void) {
    uint32_t total = 320 * 240 * 2;
    uint32_t offset = 0;

    while (offset < total) {
        uint32_t len = MIN(CHUNK_SIZE, total - offset);

        // Wait until USB is ready
        while (CDC_Transmit_FS(&frame_buffer[offset], len) == USBD_BUSY)
            ;

        offset += len;
        HAL_Delay(1); // Small delay to avoid overwhelming host
    }
}

void OV7670_HardwareReset(void) {
    HAL_GPIO_WritePin(GPIOE, OV_PWD_Pin, GPIO_PIN_RESET);

    HAL_GPIO_WritePin(GPIOE, OV_RET_Pin, GPIO_PIN_RESET);
    HAL_Delay(10);

    HAL_GPIO_WritePin(GPIOE, OV_RET_Pin, GPIO_PIN_SET);
    HAL_Delay(10);
}
uint8_t OV7670_ReadReg(uint8_t reg) {
    uint8_t data;

    HAL_I2C_Master_Transmit(&hi2c2, OV7670_ADDR, &reg, 1, HAL_MAX_DELAY);

    HAL_I2C_Master_Receive(&hi2c2, OV7670_ADDR, &data, 1, HAL_MAX_DELAY);

    return data;
}
void OV7670_WriteReg(uint8_t reg, uint8_t value) {
    uint8_t data[2] = {reg, value};

    HAL_I2C_Master_Transmit(&hi2c2, OV7670_ADDR, data, 2, HAL_MAX_DELAY);
}

static void OV7670_Init_QVGA_RGB565(void) {
    OV7670_WriteReg(0x12, 0x80); // Reset all registers
    HAL_Delay(100);
    /*j
    OV7670_WriteReg(0x11, 0x01);
    OV7670_WriteReg(0x12, 0x00);
    OV7670_WriteReg(0x0C, 0x04);
    OV7670_WriteReg(0x3E, 0x19);
    OV7670_WriteReg(0x70, 0x3A);
    OV7670_WriteReg(0x71, 0x35);
    OV7670_WriteReg(0x72, 0x11);
    OV7670_WriteReg(0x73, 0xF1);
    OV7670_WriteReg(0xA2, 0x02);
    */
    // Temporary Stopping
    OV7670_WriteReg(0x12, 0x14); // Set to QVGA and RGB output. RGB565 will be configured after
    OV7670_WriteReg(0x0C, 0x06);
    OV7670_WriteReg(0x11,
                    0b01000001); // 0x80 || 0x00 for default value OR'd with no scaling on PCLK
    OV7670_WriteReg(0x3E, 0x18);
    OV7670_WriteReg(0x40, 0xD0);
    OV7670_WriteReg(0x70, 0x3A);
    OV7670_WriteReg(0x71, 0x35);
    OV7670_WriteReg(0x72, 0x11);
    OV7670_WriteReg(0x73, 0xF8);
    OV7670_WriteReg(0x8C, 0x00);
    OV7670_WriteReg(0xA2, 0x02);

    OV7670_WriteReg(0x17, 0x16);
    OV7670_WriteReg(0x18, 0x04);
    OV7670_WriteReg(0x32, 0x00);

    OV7670_WriteReg(0x19, 0x02);
    OV7670_WriteReg(0x1A, 0x7A);
    OV7670_WriteReg(0x03, 0x0A);
}

static void OV7670_BarsTest() {
    // OV7670_WriteReg(0x12, 0x16); // Set to QVGA and RGB output. RGB565 will be configured after
    uint8_t com17 = OV7670_ReadReg(0x42);
    OV7670_WriteReg(0x42, com17 | 0x08);
}

/*
static void OV7670_Init_QVGA_RGB565(void) {
    OV7670_WriteReg(0x12, 0x80); // Reset all registers

    OV7670_WriteReg(0x12, 0x80);
    HAL_Delay(100);

    OV7670_WriteReg(0x12, 0x14);
    OV7670_WriteReg(0x40, 0xD0);
    OV7670_WriteReg(0x8C, 0x00);
    OV7670_WriteReg(0x3A, 0x04);

    OV7670_WriteReg(0x17, 0x16);
    OV7670_WriteReg(0x18, 0x04);
    OV7670_WriteReg(0x32, 0x80);

    OV7670_WriteReg(0x19, 0x02);
    OV7670_WriteReg(0x1A, 0x7A);
    OV7670_WriteReg(0x03, 0x0A);

    OV7670_WriteReg(0x0C, 0x00);
    OV7670_WriteReg(0x3E, 0x00);

    OV7670_WriteReg(0x70, 0x3A);
    OV7670_WriteReg(0x71, 0x35);
    OV7670_WriteReg(0x72, 0x11);
    OV7670_WriteReg(0x73, 0xF0);

    OV7670_WriteReg(0xA2, 0x02);

    OV7670_WriteReg(0x11, 0x01);

    HAL_Delay(50);
}
*/

/* USER CODE END 4 */

/* MPU Configuration */

void MPU_Config(void) {
    MPU_Region_InitTypeDef MPU_InitStruct = {0};

    /* Disables the MPU */
    HAL_MPU_Disable();

    /** Initializes and configures the Region and the memory to be protected
     */
    MPU_InitStruct.Enable = MPU_REGION_ENABLE;
    MPU_InitStruct.Number = MPU_REGION_NUMBER0;
    MPU_InitStruct.BaseAddress = 0x0;
    MPU_InitStruct.Size = MPU_REGION_SIZE_4GB;
    MPU_InitStruct.SubRegionDisable = 0x87;
    MPU_InitStruct.TypeExtField = MPU_TEX_LEVEL0;
    MPU_InitStruct.AccessPermission = MPU_REGION_NO_ACCESS;
    MPU_InitStruct.DisableExec = MPU_INSTRUCTION_ACCESS_DISABLE;
    MPU_InitStruct.IsShareable = MPU_ACCESS_SHAREABLE;
    MPU_InitStruct.IsCacheable = MPU_ACCESS_NOT_CACHEABLE;
    MPU_InitStruct.IsBufferable = MPU_ACCESS_NOT_BUFFERABLE;

    HAL_MPU_ConfigRegion(&MPU_InitStruct);
    /* Enables the MPU */
    HAL_MPU_Enable(MPU_PRIVILEGED_DEFAULT);
}

/**
 * @brief  This function is executed in case of error occurrence.
 * @retval None
 */
void Error_Handler(void) {
    /* USER CODE BEGIN Error_Handler_Debug */
    /* User can add his own implementation to report the HAL error return state */
    __disable_irq();
    while (1) {
    }
    /* USER CODE END Error_Handler_Debug */
}
#ifdef USE_FULL_ASSERT
/**
 * @brief  Reports the name of the source file and the source line number
 *         where the assert_param error has occurred.
 * @param  file: pointer to the source file name
 * @param  line: assert_param error line source number
 * @retval None
 */
void assert_failed(uint8_t* file, uint32_t line) {
    /* USER CODE BEGIN 6 */
    /* User can add his own implementation to report the file name and line number,
       ex: printf("Wrong parameters value: file %s on line %d\r\n", file, line) */
    /* USER CODE END 6 */
}
#endif /* USE_FULL_ASSERT */

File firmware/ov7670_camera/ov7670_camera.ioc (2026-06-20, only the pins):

Mcu.UserName=STM32F765VITx
PA11.Signal=USB_OTG_FS_DM
PA12.Signal=USB_OTG_FS_DP
PA13.Signal=SYS_JTMS-SWDIO
PA14.Signal=SYS_JTCK-SWCLK
PA4.Signal=DCMI_HSYNC
PA6.Signal=DCMI_PIXCLK
PA8.GPIO_Label=OV_XCLK
PA8.Signal=RCC_MCO_1
PB10.Signal=I2C2_SCL
PB11.Signal=I2C2_SDA
PB7.Signal=DCMI_VSYNC
PC6.Signal=DCMI_D0
PC7.Signal=DCMI_D1
PC8.Signal=DCMI_D2
PD3.Signal=DCMI_D5
PE1.Signal=DCMI_D3
PE10.GPIO_Label=OV_RET
PE10.Signal=GPIO_Output
PE11.GPIO_Label=OV_PWD
PE11.Signal=GPIO_Output
PE4.Signal=DCMI_D4
PE5.Signal=DCMI_D6
PE6.Signal=DCMI_D7
PH0/OSC_IN.Signal=RCC_OSC_IN
PH1/OSC_OUT.Signal=RCC_OSC_OUT

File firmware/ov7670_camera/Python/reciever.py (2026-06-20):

import serial
import os
from datetime import datetime as dt
import numpy as np
from PIL import Image

# ============================================================
# CONFIGURATION
# ============================================================

PORT = "/dev/ttyACM1"      # Linux
# PORT = "COM5"           # Windows

BAUDRATE = 115200

WIDTH = 320
HEIGHT = 240

FRAME_SIZE = WIDTH * HEIGHT * 2

INIT_MESSAGE = "Sending Frame!!!!!!"
INIT_MSG_LEN = len(INIT_MESSAGE)

RECIEVED_SIZE = FRAME_SIZE + INIT_MSG_LEN

# ============================================================
# OPEN SERIAL PORT
# ============================================================

print(f"Opening {PORT}...")

ser = serial.Serial(
    PORT,
    BAUDRATE,
    timeout=10
)

print("Waiting for frame...")

# ============================================================
# FIND FRAME START MARKER
# ============================================================

MARKER = b"!!!!!!"

print("Waiting for frame marker...")

window = bytearray()

while True:
    b = ser.read(1)

    if not b:
        raise RuntimeError("Timeout waiting for marker")

    window.extend(b)

    if len(window) > len(MARKER):
        window.pop(0)

    if bytes(window) == MARKER:
        print("Marker found")
        break

# ============================================================
# RECEIVE FRAME
# ============================================================

frame = bytearray()

while len(frame) < FRAME_SIZE:

    chunk = ser.read(FRAME_SIZE - len(frame))

    if not chunk:
        raise RuntimeError(
            f"Timeout after receiving {len(frame)} bytes"
        )

    frame.extend(chunk)

    print(
        f"\rReceived {len(frame):6d}/{FRAME_SIZE}",
        end="",
        flush=True
    )

print("\nFrame received!")

# ============================================================
# DEBUG
# ============================================================

print("First 32 bytes:")
print(frame[:32].hex())

# ============================================================
# RGB565 -> RGB888
# ============================================================

# OV7670 RGB565 interpreted as:
#
# Byte0 = MSB
# Byte1 = LSB
#
# RGB565:
# RRRRRGGGGGGBBBBB

data = np.frombuffer(frame, dtype=">u2") # Big endian output, so no reversal of byte order
# data = np.frombuffer(frame, dtype="<u2")

r = (data >> 11) & 0x1F
g = (data >> 5) & 0x3F
b = data & 0x1F

# Expand to full 8-bit precision

r = (r << 3) | (r >> 2)
g = (g << 2) | (g >> 4)
b = (b << 3) | (b >> 2)

rgb = np.stack((r, g, b), axis=-1).astype(np.uint8)

rgb = rgb.reshape((HEIGHT, WIDTH, 3))

# ============================================================
# SAVE IMAGE
# ============================================================

img = Image.fromarray(rgb, "RGB")

t = dt.now().strftime("%Y%m%d_%H%M%S")
capture_dir = os.path.expanduser("~/PersonalProjects/kamikaze-drone/firmware/ov7670_camera/Python/captures")
os.makedirs(capture_dir, exist_ok=True)
img.save(os.path.join(capture_dir, f"{t}.png"))

print("Saved capture.png")

img.show()

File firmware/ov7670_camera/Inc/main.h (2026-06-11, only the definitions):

#define OV_RET_Pin GPIO_PIN_10
#define OV_RET_GPIO_Port GPIOE
#define OV_PWD_Pin GPIO_PIN_11
#define OV_PWD_GPIO_Port GPIOE
#define OV_XCLK_Pin GPIO_PIN_8
#define OV_XCLK_GPIO_Port GPIOA

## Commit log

2026-04-01 finished stm32f7 breakout board
    [breakout_board_bom.csv, breakout_board_bom.xlsx, connectors.kicad_sch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]
2026-04-06 added lsm6dsl to pcb and ordered v3
    [breakout_board_bom.csv, breakout_board_bom.xlsx, connectors.kicad_sch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]
2026-04-12 final breakout board ordered
    [microcontroller.kicad_sch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]
2026-04-17 Updated titleblock on f765 breakout pcb
    [connectors.kicad_sch, microcontroller.kicad_sch, power_regulation.kicad_sch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]
2026-05-01 Added on board LED to PCB and blinky for board
    v6 of the PCB now has an in built on board LED to PE02, to allow for
    faster debugging.
    The first assembled prototype finally worked, and a blinky sketch was
    flashed to test. Relevant code has been added to firmware.
    [breakout_board_bom.xlsx, microcontroller.kicad_sch, peripherals.kicad_sch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]
2026-05-23 v1 of PCB completed
    Complete schematic completed with motor drivers, sensor integration and
    others.
    [kamikaze-drone.kicad_pcb, kamikaze-drone.kicad_sch, motor_drivers.kicad_sch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]
2026-05-24 New layout for pcb
    [kamikaze-drone.kicad_pcb]
2026-05-24 WIP - arranging components in updated PCB
    [kamikaze-drone.kicad_pcb, power_management.kicad_sch, stm32f7_main_sheeet.kicad_sch]
2026-05-24 WIP - Power routing done. Signal routing remaining
    - Power routing from USB and battery to MCP and AMS completed.
    - Power routing from motors to battery completed
    - Grounds have not been routed yet, leaving to the end.
    - Most 3V3 pads haven't been routed yet, leaving to the end
    [kamikaze-drone.kicad_pcb, stm32f7_main_sheeet.kicad_sch]
2026-05-24 v2.0 of PCB completed
    Updated routing to have USB port in center of top.
    Shrank overall size to 50x50 mm
    Layout is now ground+signal >> ground >> 3V3 >> signal
    TODO: Add stitching vias between ground on top and second layer?
    [kamikaze-drone.kicad_pcb, kamikaze-drone.kicad_sch, motor_drivers.kicad_sch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]
2026-05-27 add: added images and updated readme
    - Removed redundant schematic files.
    - Added images of v2 of the PCB
    - Updated readme to include hardware design
    [sensors.kicad_sch, stm32f4_main_sheet.kicad_sch]
2026-05-27 add: added watermark to pcb
    [kamikaze-drone.kicad_pcb]
2026-05-28 feat: added touch points to PCB
    Took advice from reddit to improve the PCB schematic
    [kamikaze-drone.kicad_pcb, peripherals.kicad_sch, power_management.kicad_sch]
2026-06-03 v3 of PCB made. ov7670 implementation guide added
    [kamikaze-drone.kicad_pcb, motor_drivers.kicad_sch, power_management.kicad_sch]
2026-06-11 firmware: added ov7670 camera support and updated gitignore
    [kamikaze-drone.kicad_pcb]
2026-06-11 fw: ov7670 camra colors corrected
    [main.c, reciever.py]

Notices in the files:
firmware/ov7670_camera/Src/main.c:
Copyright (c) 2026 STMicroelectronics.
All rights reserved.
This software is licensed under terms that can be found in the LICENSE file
